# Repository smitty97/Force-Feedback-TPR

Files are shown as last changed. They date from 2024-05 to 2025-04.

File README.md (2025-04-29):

# Force-Feedback-TPR
VPForce FFB Mod for Thrustmaster TPR Rudder Pedals

A62D62CD-0B10-464C-B153-7518431104F6_1_105_c

These parts are for converting your Thrustmaster TPR pedals with a 86BLF04 kit from https://vpforcecontrols.com.  The mod does not permanently change anything on the pedals, there is no cutting, and you could revert it back to original stock if desired.  The geometry of the cable run is set up so that it will not go slack in any position.  Now, i made my parts out of aluminum and did the tensioning a bit different but have redesigned them slightly so that they can be 3d printed as well.  It might work, You'll just have to try it.  If you can make them with aluminum even better.  The motor pulley should definitely be metal of some kind though.  NOTE - TPR_pulley_0.9 is just a bit smaller in diameter, made from 1" round stock.  This is probably the better pulley to make, as it will use more of the motor range and be a bit stronger.  My 86BLF04 can push each foot with about 20lbf/9kgf so be sure to bolt the pedals down relative to your chair.

This will take some DIY skills, it's not print-and-be-done, but it's close.

Some of the parts used:

1 - 86BLF04 x1 DIY Kit from https://vpforcecontrols.com 

1 - https://www.amazon.com/gp/product/B013ETVO12 24V 350W power supply

2 - https://www.amazon.com/gp/product/B077K7KNX9 pack of 2

2 - https://www.amazon.com/gp/product/B000COCQ06 pack of 2

2 - https://www.mcmaster.com/catalog/90220A130 each

4 - https://www.mcmaster.com/catalog/91920A710 each

2 - https://www.mcmaster.com/catalog/2705T132 each

4 - https://www.mcmaster.com/catalog/92510A765 each

4 - https://www.mcmaster.com/8920N36/  each

8 - https://www.mcmaster.com/91294A212/ (box of 100)

4 - https://www.mcmaster.com/91290A252/ (box of 50)

2 - https://www.mcmaster.com/94105A534/ (box of 50)

2 - https://www.mcmaster.com/91294A253/ (box of 25)

2 - https://www.mcmaster.com/94645A205/ (box of 100)

1 - https://www.amazon.com/USAMILY-Stainless-Aluminum-Sleeves-Thimbles/dp/B0CKPHJG3F 

Assembly steps:
1. Remove the spring system from the rear of the TPR's. There are 4 M5 flatheads holding it onto the back,  Remove the bottom end of the links to the original teeter arm (save the pins, plastic bushings, e-clips)
2. Open up the electronics area on the back, remove the wire going to the teeter hall sensor
3. The original teeter has a hinge pin and long bolt, you will need it, disassemble from spring assembly.
4. Make sure you know where the center of rotation is on the motor.  Hook it up, set endpoints at 0 to 4096 and turn on the spring.  mark the shaft and base with a sharpie so you can line them up when unpowered.
5. Assemble the motor to the plate, and add the long spacers.  Put the back plate on loosely so you can slip in the teeter hinge pin into its counterbores.  You'll want to have 2 or 3 spacer washers on each side of the teeter.  Press in new hinge bushings into the teeter.
6. With the teeter in place, fully clamp together the long spacers.  Use the original long bolt thru the teeter hinge tube.
7. Add the pulleys and spacers to each side
8. Screw in the bolts with the vent hole all the way down into the teeter arm.  we will be raising them up to tension the cable later.  If using a 3d print, you might want to also use some thin 1/4-20 nuts so the thread doesnt strip out.
9. This is the tricky part- the cable.  It's thick, and resistant to bends, and might take 3 or 4 hands to get it wrapped right.  also clip off the ball on the end but be careful not to let it unravel too much.  pass it thru the hole in the motor pulley so half remains on each side.  without letting the pulley spin (power it up or use a allen key to stop it)  wind 2 wraps toward the motor and then to a pulley and up thru the vented arm bolt.  put on a cable stop to keep it there.  careful!  letting go at any time and it all unwinds.  do the same on the other side, but go away from the motor.  see pics on how it should look
   *****  NOTE- new 304 1/16 7x7 wire rope item B0CKPHJG3F is much easier to work with.  the brake cable seems to shred itself over time.
10. Center up the motor to your sharpie marks.  tighten/loosen the cable stops so that the arm is level with the motor centered.  alternate from side to side, making it tighter each time.  make sure the wrap on the pulley isn't crossing over itself.
11. fully tighten the cable stops with a wrench.  then, raise each vented bolt to really tension the cable.  It should almost guitar-string-tight.
12. FFB unit is done!  Now just mount it to the back of the TPR. It'll be best to use a ball-end hex wrench to get to some of the bolts, thru the holes in the front plate.
13. Transfer over the link bushings and pins from the original teeter arm.
14. Print the USB Box & Lid, mount the kit USB board inside and wire up.
15. Install VPForce Configurator and the WIP version of VPForce TelemFFB.
16. enjoy!
17. These instructions and models provided as-is.   DIY!

Also check out the load cell brake mod! https://github.com/smitty97/Load-Cell-Brakes-TPR

First prototype, some parts may differ from supplied files:





Other builds:

by @SR-F_Winger_[73]_David:





3D Printed version by @Toddimus:




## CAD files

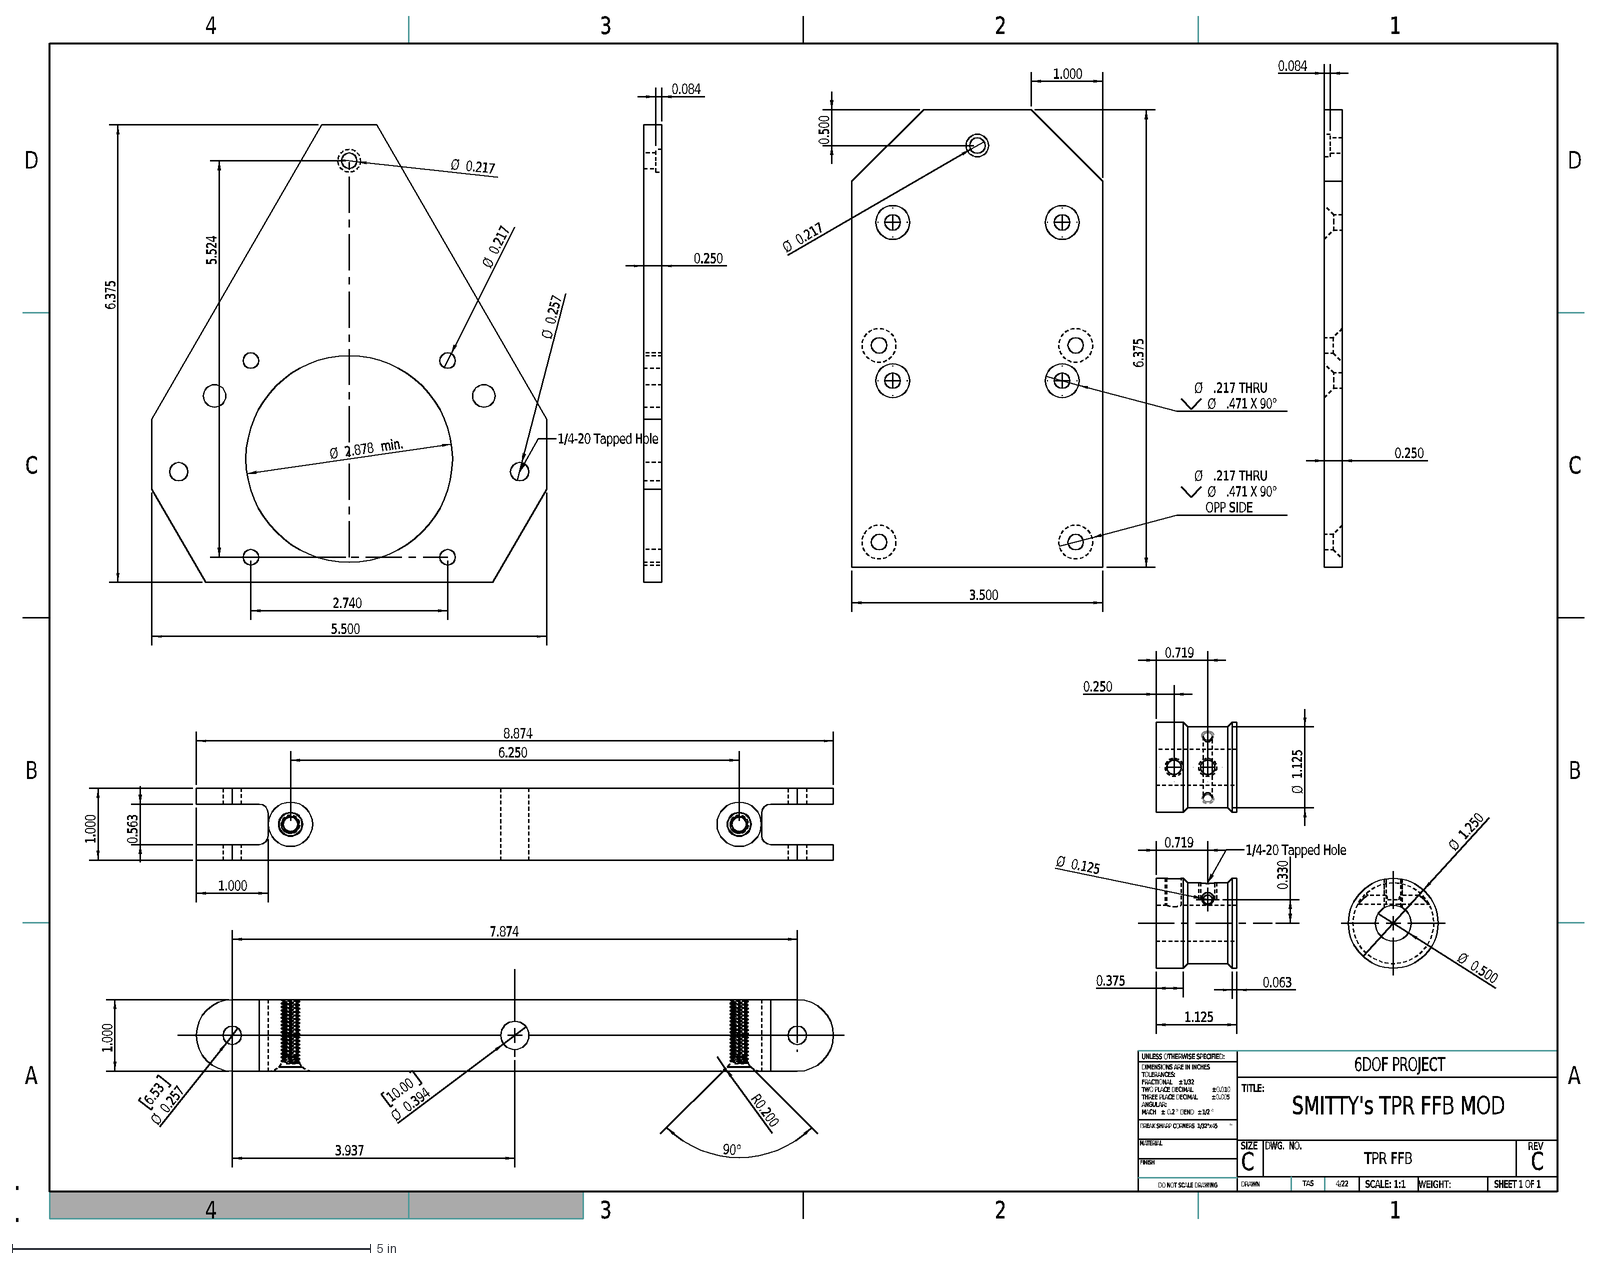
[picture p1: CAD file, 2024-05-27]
TPR_FFB-REVC.dxf
SMITTY's TPR FFB MOD
C
DO NOT SCALE DRAWING
TPR FFB
SHEET 1 OF 1
4/22
TAS
UNLESS OTHERWISE SPECIFIED:
SCALE: 1:1
WEIGHT:
REV
DWG. NO.
SIZE
TITLE:
6DOF PROJECT
DRAWN
FINISH
MATERIAL
BREAK SHARP CORNERS 1/32"x45
°
DIMENSIONS ARE IN INCHES
TOLERANCES:
FRACTIONAL
±
1/32
TWO PLACE DECIMAL
0.010
THREE PLACE DECIMAL
0.005
ANGULAR:
MACH
0.2
BEND
1/2
A
B
D
4
3
2
1
3.500
6.375
1.000
0.500
Ø
.217 THRU
.471 X 90°
OPP SIDE
0.217
5.524
2.740
2.878
min.
5.500
0.257
1/4-20 Tapped Hole
0.084
0.250
7.874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

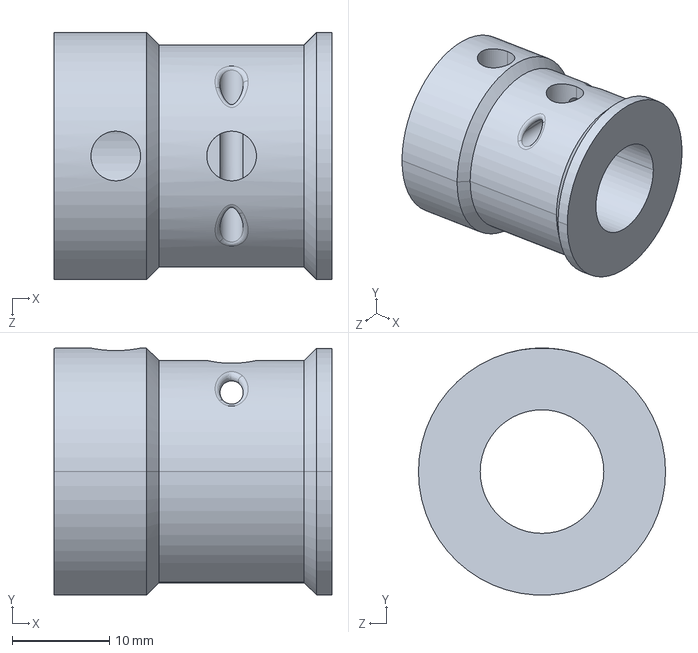
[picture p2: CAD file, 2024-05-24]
TPR_pulley_0.9.STEP
28.6 x 25.4 x 25.4 mm

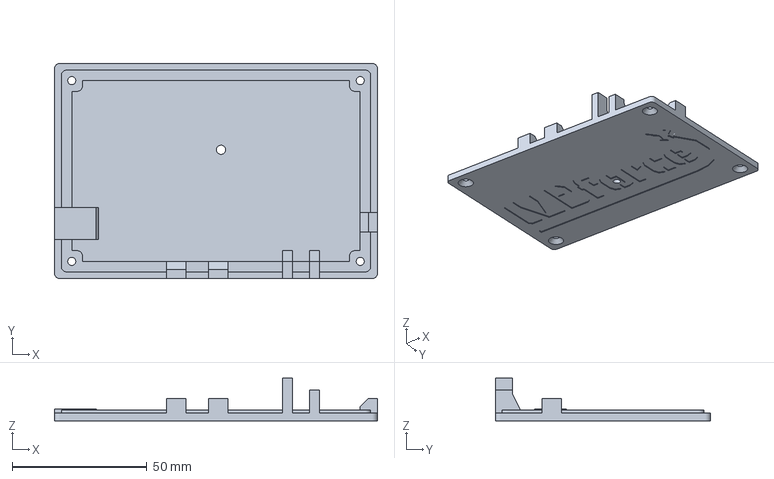
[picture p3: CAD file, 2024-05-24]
TPR USB Lid_MMU.3mf
120.0 x 80.0 x 15.9 mm

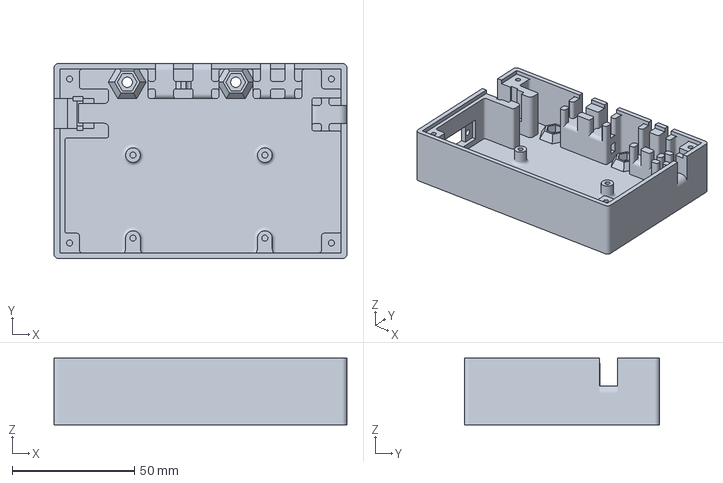
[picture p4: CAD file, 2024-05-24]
TPR USB Bottom.3mf
120.0 x 80.0 x 27.3 mm

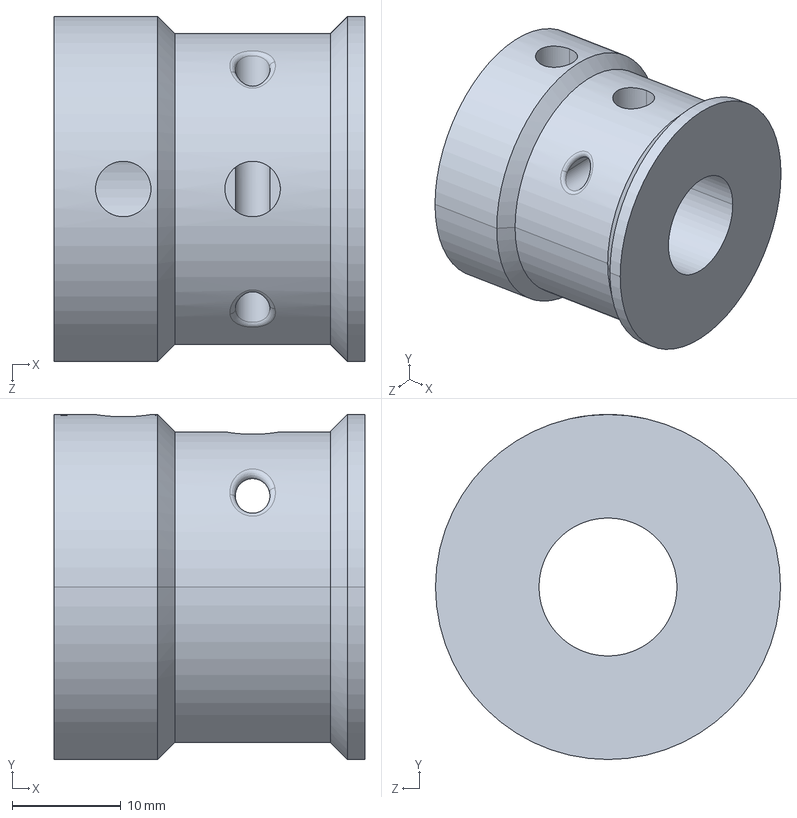
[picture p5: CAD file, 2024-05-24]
TPR_pulley.STEP
28.6 x 31.8 x 31.8 mm

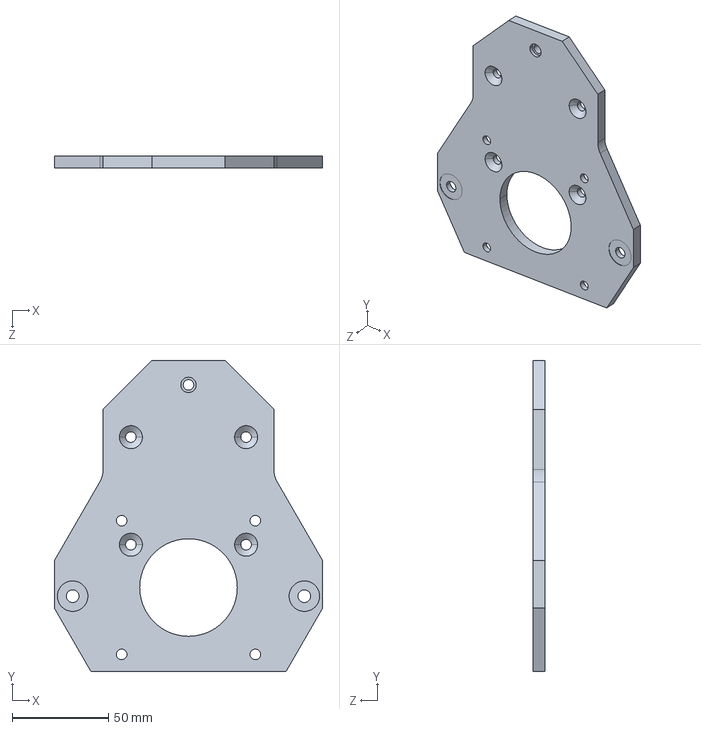
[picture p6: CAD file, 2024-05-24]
TPR_ffb_mount_plate_1.STEP
139.7 x 161.9 x 6.35 mm

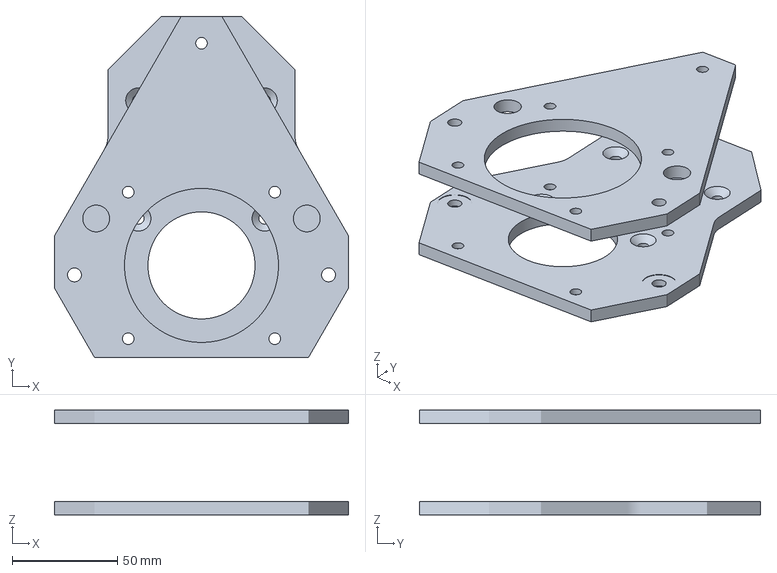
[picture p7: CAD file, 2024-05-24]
TPR_ffb_mount_plates_3dprint.3MF
139.7 x 161.9 x 49.7 mm

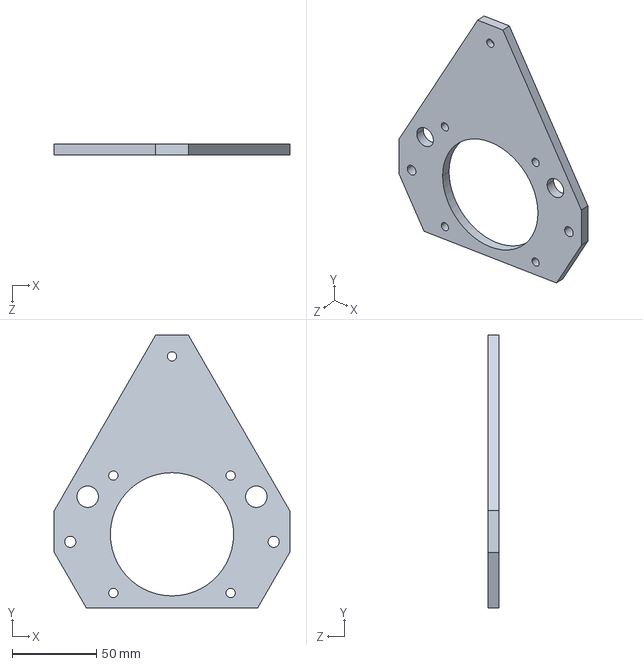
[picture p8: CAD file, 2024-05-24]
TPR_ffb_mount_plate_2.STEP
139.7 x 161.9 x 6.35 mm

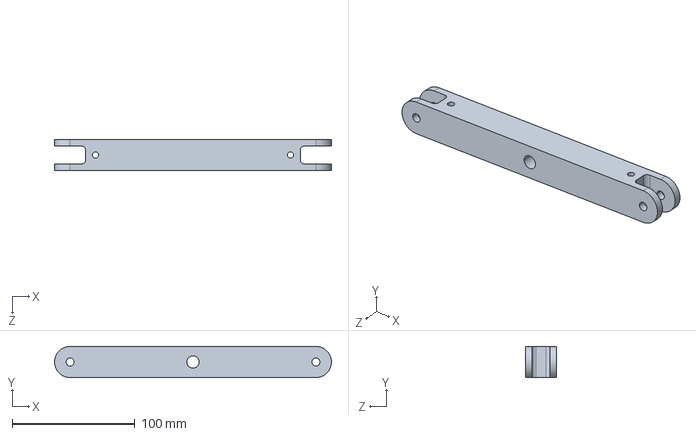
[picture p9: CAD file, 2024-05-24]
TPR_ffb_teeter_arm_no_threads.STEP
225.4 x 25.4 x 25.4 mm

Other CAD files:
TPR_ffb_teeter_arm_3dprint.3MF
TPR_FFB_Kit_3dprint.x_t

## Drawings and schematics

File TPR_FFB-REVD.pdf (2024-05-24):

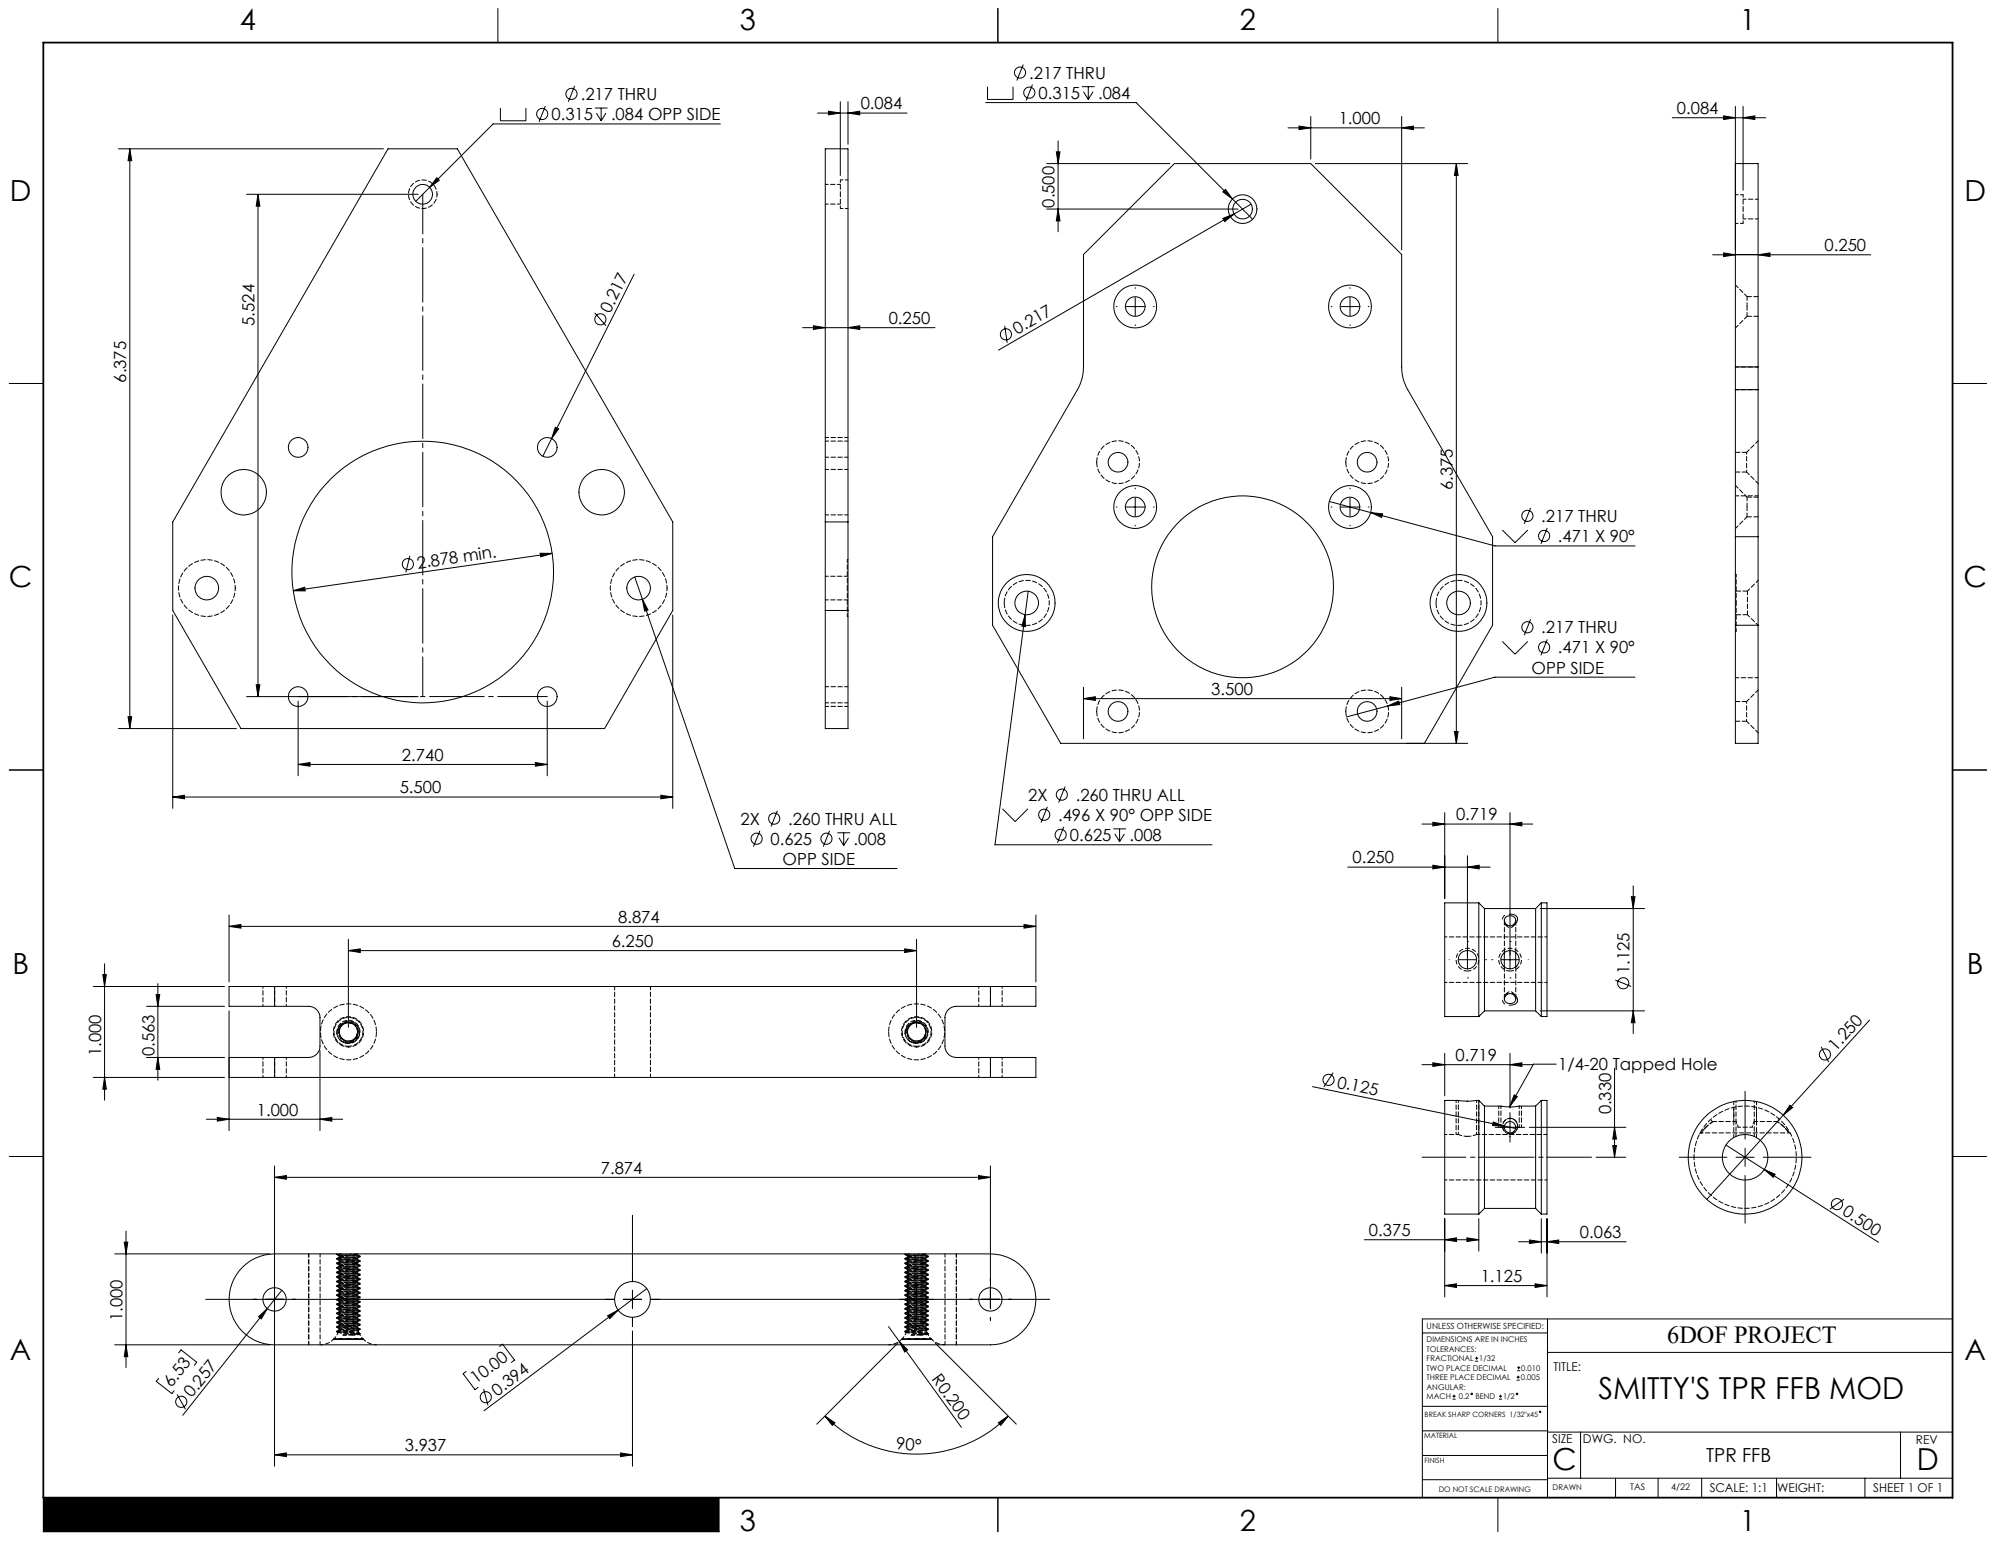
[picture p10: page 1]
.217 THRU .471 X 90°; .217 THRU .471 X 90° OPP SIDE; .260 THRU ALL; .496 X 90° OPP SIDE 0.625 .008; .217 THRU 0.315 .084; 2.878 min.; OPP SIDE; .217 THRU 0.315 .084 OPP SIDE; 1/4-20 Tapped Hole; TPR FFB; DWG. NO.; REV; TWO PLACE DECIMAL

UNLESS OTHERWISE SPECIFIED:
DIMENSIONS ARE IN INCHES
TOLERANCES:
FRACTIONAL 1/32
THREE PLACE DECIMAL 0.005
ANGULAR:
MACH 0.2 BEND 1/2
BREAK SHARP CORNERS 1/32"x45

6DOF PROJECT
SMITTY'S TPR FFB MOD

DO NOT SCALE DRAWING | DRAWN | TAS | 4/22 | SCALE: 1:1 | WEIGHT: | SHEET 1 OF 1

SOLIDWORKS Educational Product. For Instructional Use Only. 4
